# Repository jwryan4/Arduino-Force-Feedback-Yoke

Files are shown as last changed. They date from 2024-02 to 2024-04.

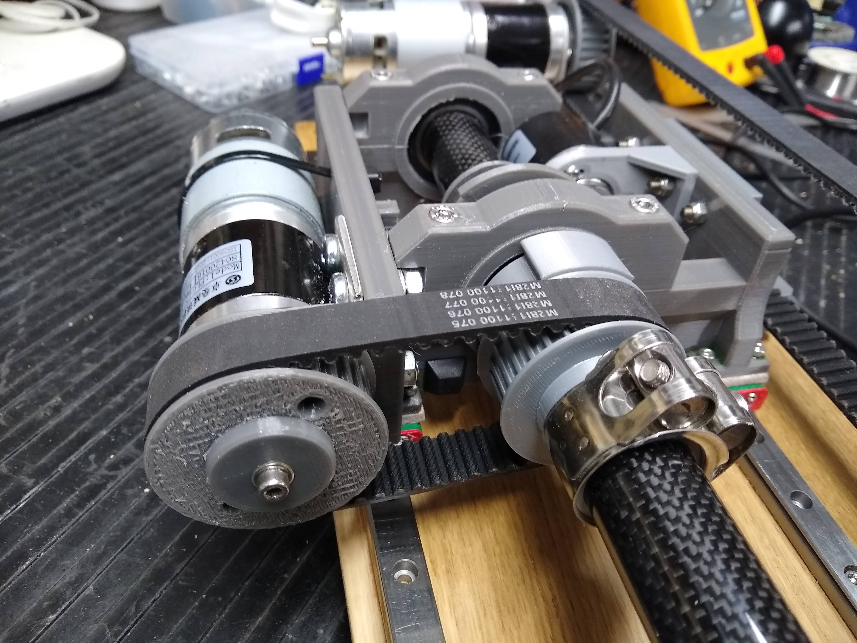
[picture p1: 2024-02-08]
Photos/IMG_20231003_192117274.jpg

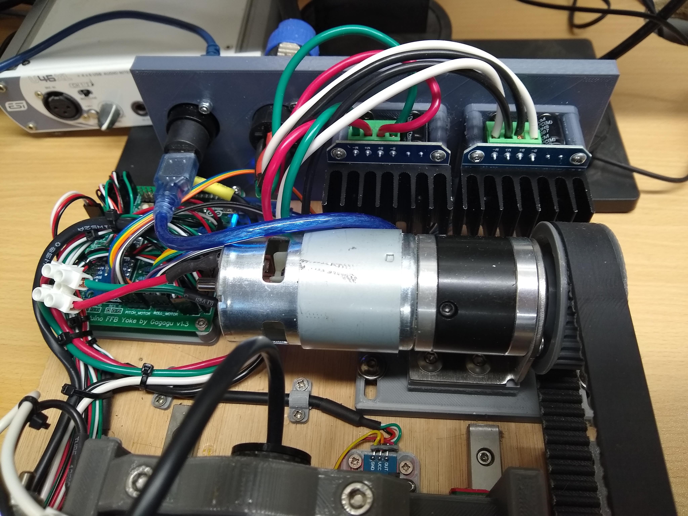
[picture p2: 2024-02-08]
Photos/IMG_20240125_142316894.jpg

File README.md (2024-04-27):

# Arduino-Force-Feedback-Yoke "NOT THE ORIGNIAL PROJECT!! THAT'S HERE: https://github.com/jwryan4/Arduino-Force-Feedback-Yoke"
CAD Files for GAGAGU FFB Flight Sim Yoke

I am going to try and update as much as I can so that We have everything needed to complete the new V2 project. 

I am not the create nor the designer of this project all credit goes to the wonderful creators https://github.com/jwryan4 & https://github.com/gagagu

They have done some amazing work and this is just me trying to make it easier for us as plebs to create their awesome project

One of the massive changes is the arrival of the rotary encoders. 

I am not as smart as I would like to be when it comes to making theses kinds of things but JR4 is, the way you need to wire the new encoders to the exsiting circutry is as follows and I Quote:

"There is no need for centre posn sensors as the rotary encoders provide better tracking accuracy than previous versions (v1.x). Use the same pcb. Rotary encoders connect to pin headers ROLL 1/ROLL 2 and PITCH1/PITCH2.  My encoders have 4 wires, BLK (gnd), RED (+V), GRN (phase1 out), WHT (phase2 out).  Connect GRN to PITCH1/ROLL1, WHT to PITCH2/ROLL2." - JR4

This one line of information is what should be able to take you from V1.3 to V2!!

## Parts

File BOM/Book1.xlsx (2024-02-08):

BOM List for GAGAGU FFB Yoke version 2
Description | Qty | Detail | Hyperlink | Price | Total
 |  |  |  | £
Mechanical
RS775 motor | 2 | Available from Amazon (same spec available many suppliers ) | Link (https://www.amazon.co.uk/gp/product/B075D85KVV/ref=ppx_yo_dt_b_search_asin_title?ie=UTF8&psc=1) | 12.99 | 25.98
Motor Bracket |  | Available from Aliexpress | Link (https://www.aliexpress.com/item/1005003394995769.html?spm=a2g0o.cart.0.0.5f2738daYltizJ&mp=1) | 8.39 | 8.39
Planetary Gearbox, Pitch (see note 1 below) | 1 | PLG42-16G, 42mm, 4:1, 10mm keyed output shaft with 5mm pinion gear for input | Link (https://www.amazon.co.uk/dp/B0BTY4VBBQ/?coliid=I15R9M6IFE6G61&colid=11U0ZQFTY1AUE) | 61.21 | 61.21
Planetary Gearbox, Roll (see note 1 below) | 1 | PLG42-16G, 42mm, 20:1, 10mm keyed output shaft with 5mm pinion gear for input | Link (https://www.amazon.co.uk/dp/B0BVQML11F/?coliid=I15R9M6IFE6G61&colid=11U0ZQFTY1AUE) | 74.66 | 74.66
Precision Quadrature Rotary Encoder | 2 | 600ppr (various suppliers) | Link (https://www.ebay.co.uk/itm/204516788210) | 12.72 | 25.44
Corbon Fibre Yoke Column | 1 | 25mm OD, 23mm ID, 300mm length | Link (https://www.amazon.co.uk/gp/product/B017XEAMUI/ref=ppx_yo_dt_b_search_asin_title?ie=UTF8&psc=1) | 14.19 | 14.19
Yoke Column Bearing (pair) | 1 | 6905-2RS, 42mm OD, 25mm ID, 9mm width | Link (sold as a pair) (https://www.ebay.co.uk/itm/266121767350) | 4.00 | 4.00
Pitch Encoder Belt Bearing (pair) | 1 | 61805-2RS, 32mm OD, 37mm ID, 7mm width | Link (sold as a pair) (https://www.ebay.co.uk/itm/266109732777) | 4.95 | 4.95
Linear Rails (see note 2 below) | 2 | Linear Rail MGN12C x 300mm (available from many suppliers) | Link (https://www.ebay.co.uk/itm/353965723573) | 17.00 | 34.00
Additional Guide (Carriage) for Linear Rails | 2 | Bearing Block MGN12C | Link (https://www.ebay.co.uk/itm/185853523677) | 6.36 | 12.72
Pitch Belt | 1 | 850-5M-15 Timing Belt | Link (https://www.bearingsrus.co.uk/850-3m-15) | 7.87 | 7.87
Roll Belt | 1 | 305-5M-15 Timing Belt | Link (https://www.bearingsrus.co.uk/305-3m-15) | 4.84 | 4.84
Roll Encoder Belt | 1 | 77T, 154mm, GT2, 6mm, 2mm pitch | Link (https://www.ebay.co.uk/itm/283194907394?var=586475426779) | 2.95 | 2.95
Picth Belt Clamp | 1 | Aluminium Timing Belt Clamp, HTD-5M 15 | Link (https://www.ebay.co.uk/itm/403912354720?var=673795213478) | 3.95 | 3.95
Yoke/ Roll drive pulley Column Clamp (pair) | 1 | Hose Clamp, Stainless Steel, 29-31mm | Link (sold as a pair) (https://www.ebay.co.uk/itm/203846963479?var=504299046223) | 9.02 | 9.02
Miscellaneous Items
Screws | Various | Price is approximate as various sizes/qty's required |  | 40.00 | 40.00
PLA+, GRY/BLK 2-pack | 1 |  | Link (https://www.amazon.co.uk/gp/product/B0B749Z8H1/ref=ppx_yo_dt_b_search_asin_title?ie=UTF8&th=1) | 38.99 | 38.99
Plywood Board, 18mm | 1 | Required for rigid base |  | 20.00 | 20.00
Plywood coard, 9mm | 1 | Required for U-shaped outer case |  | 15.00 | 15.00
 |  |  |  |  | 0.00
Electronic |  |  |  |  | 0.00
Arduino Micro | 1 |  | Link (https://www.amazon.co.uk/gp/product/B00AFY2S56/ref=ppx_yo_dt_b_search_asin_title?ie=UTF8&th=1) | 25.00 | 25.00
BTS7960 H-Bridge Motor Drivers (pair) | 1 |  | Link (sold as a pair) (https://www.amazon.co.uk/gp/product/B098WYZ9DP/ref=ppx_yo_dt_b_search_asin_title?ie=UTF8&psc=1) | 14.00 | 14.00
Power Supply, SMPS, 24 Volt, 10 Amp | 1 |  | Link (https://www.amazon.co.uk/gp/product/B09YRF3ZHR/ref=ppx_yo_dt_b_search_asin_title?ie=UTF8&psc=1) | 16.99 | 16.99
Note 1: Planetary Gearboxes
My planetary gearboxes were sourced from Aliexpress. However, the item is no longer listed (as of Jan 2024). The links above seem to be the same product from Amazon UK but at twice the price. Please be aware that you buy at your own risk. |  | I used gearboxes with a 10mm keyed output shaft because I think that a standard 6.35mm D or 8mm shaft would cause 3D printed pulleys to fail (I used PLA+). Shaft adaptors for smaller diameters are available from eBay if required. Please note that the motor pulley STL file may require modification to ensure good fit with your gear output shaft/adaptor. | Output Shaft Adaptor (https://www.ebay.co.uk/itm/155829523711)
Note 2: Linear Rails
Supplier will not ship to UK

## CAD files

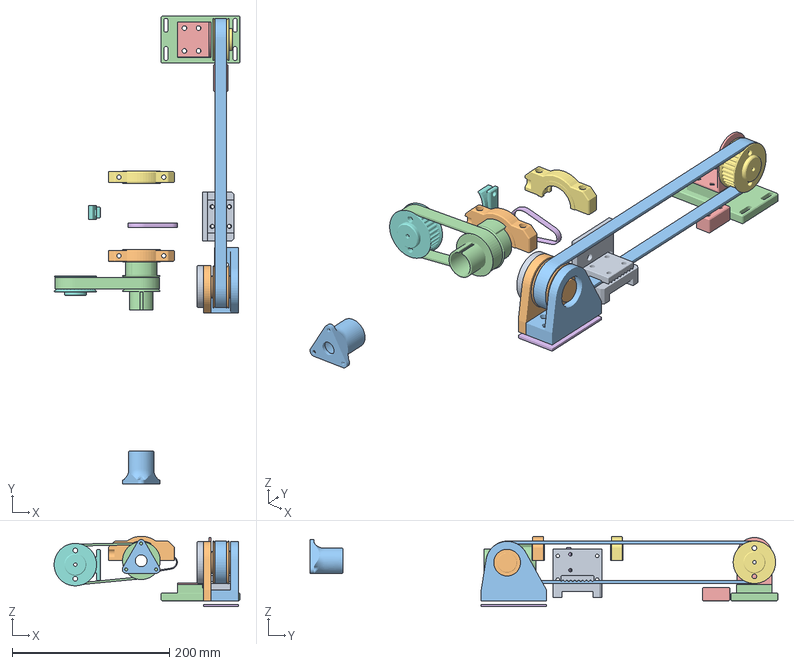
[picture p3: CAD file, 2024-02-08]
FFB_Yoke_Assembly_v2.FCStd
236.2 x 595.2 x 89.4 mm
Frame_Pitch_Belt_Clamp
Pitch_Belt
Roll_Belt
Roll Motor Mount
Roll_Encoder_Belt
Rear_Yoke_Column_Upper_Mount
Roll_Motor_Rear_Mount
Pitch Encoder Spacer
Pitch Encoder Mount
Pitch Encoder Pulley Mount
Pitch_Motor_Mount
Pitch_Rear_Stop
Pitch Encoder Pulley Mount001
HTD 32 5M 15 Pulley v8
HTD 32 5M 15 Pulley v009
Clamping_Plate v1
Pitch_Encoder_Pulley_5_15_32t v4
CadetYokev3 (1) v6
28_5M_15_Yoke_Column_Pulley v24

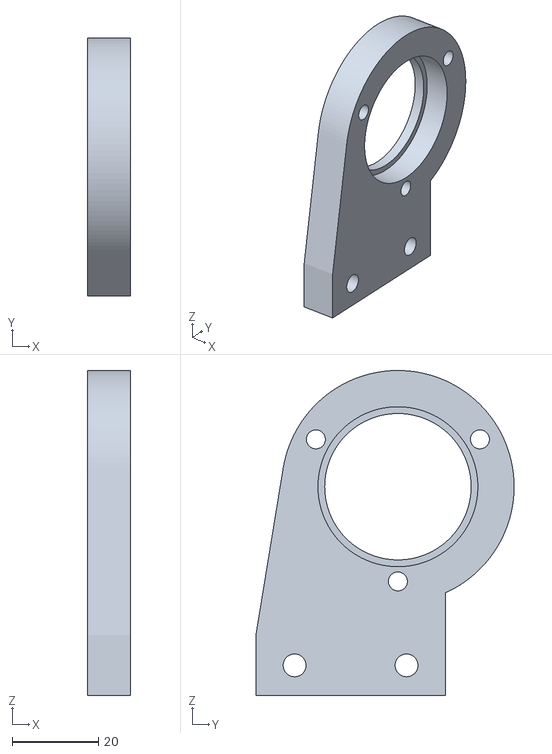
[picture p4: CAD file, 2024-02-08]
STL Files/FFB_Yoke_Assembly_v2-Pitch_Pulley_Mount_AssyPitch Encoder Mount.stl
10.0 x 60.0 x 75.5

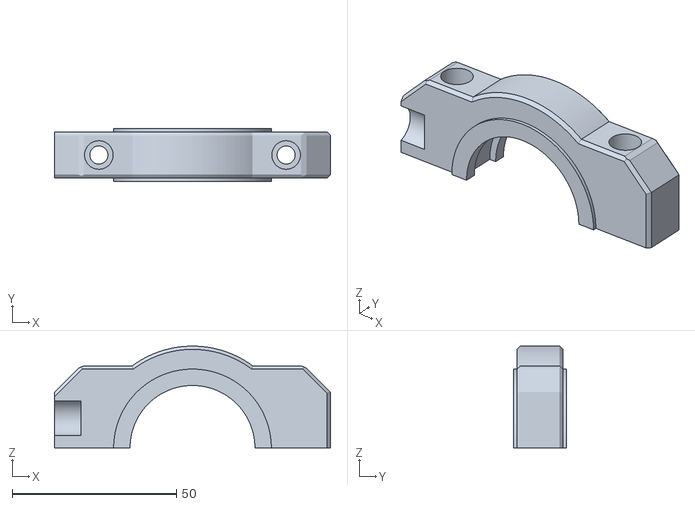
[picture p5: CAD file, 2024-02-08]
STL Files/FFB_Yoke_Assembly_v2-Rear_Yoke_Shaft_Housing_Top.stl
84.0 x 16.0 x 31.0

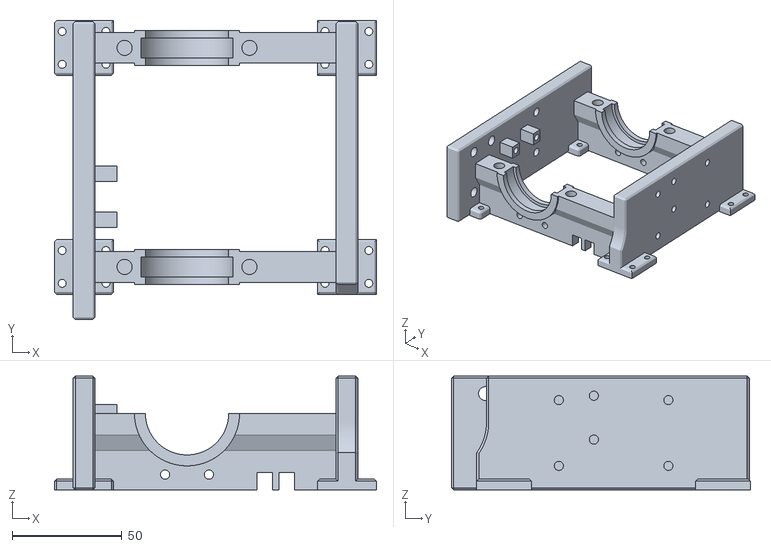
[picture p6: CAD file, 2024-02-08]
STL Files/FFB_Yoke_Assembly_v2-Frame.stl
147.0 x 136.5 x 52.0

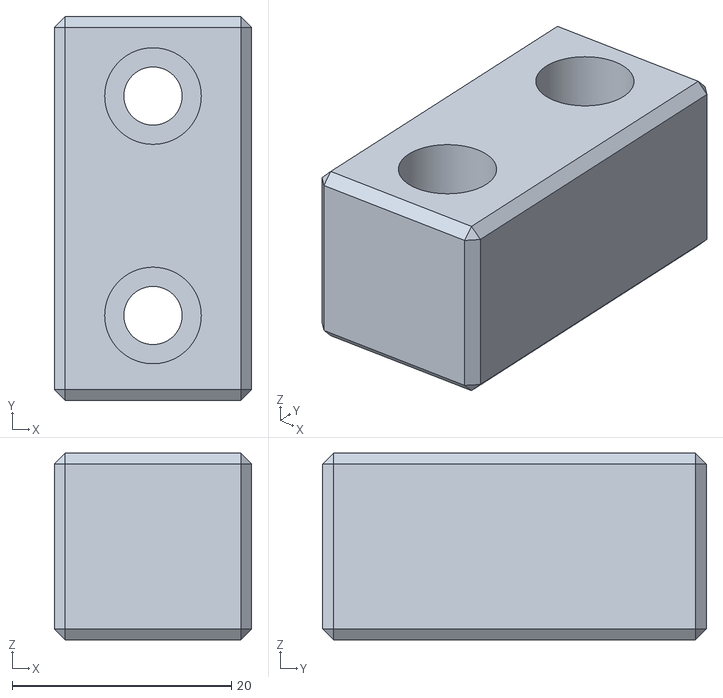
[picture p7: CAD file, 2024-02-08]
STL Files/FFB_Yoke_Assembly_v2-Pitch_Rear_Stop.stl
18.0 x 35.0 x 17.0

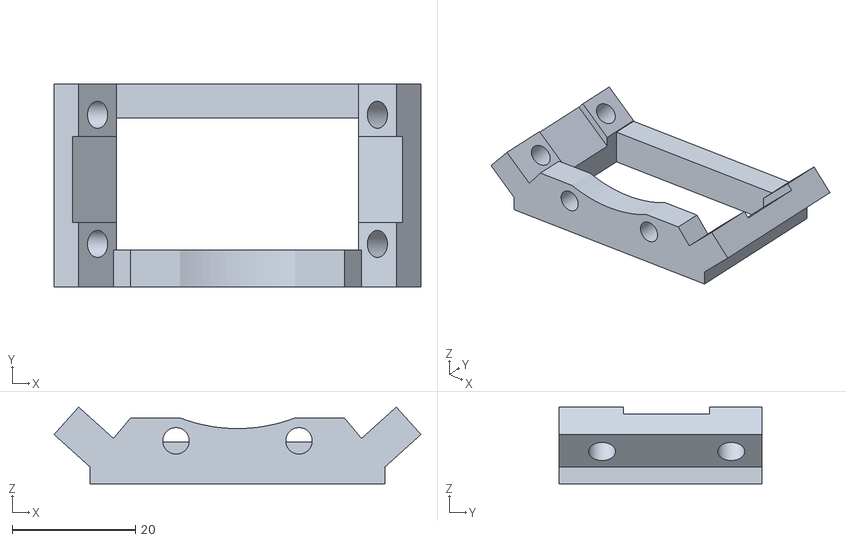
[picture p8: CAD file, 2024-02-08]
STL Files/FFB_Yoke_Assembly_v2-Frame_Roll_IR_Sensor_Mount.stl
59.7 x 33.0 x 12.5

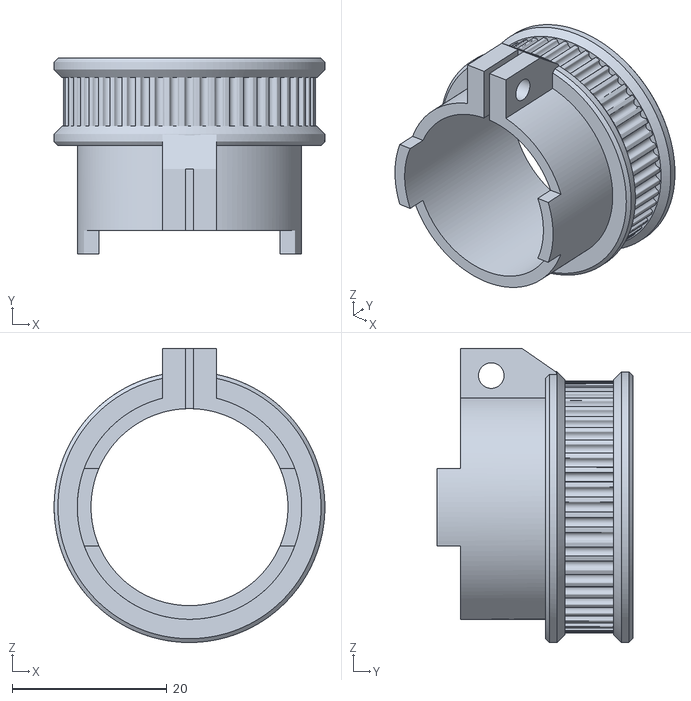
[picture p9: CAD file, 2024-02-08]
STL Files/FFB_Yoke_Assembly_v2-Yoke_Roll_Encoder_Pulley.stl
35.0 x 25.3 x 38.0

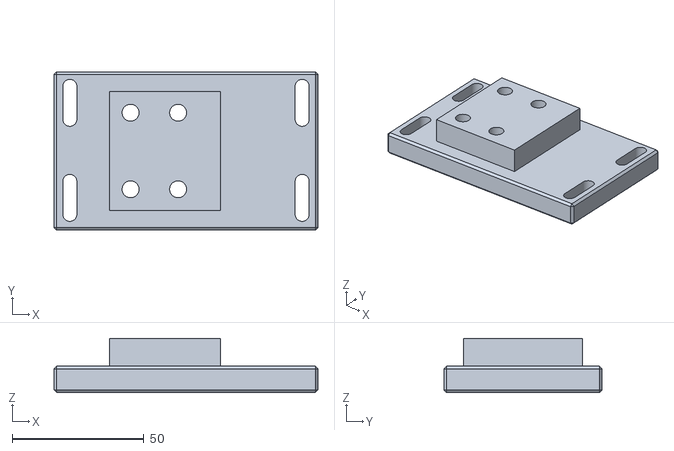
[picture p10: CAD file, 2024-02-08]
Misc STL Files/FFB_Yoke_Assembly_v2-Pitch_Motor_Mount.stl
100.0 x 60.0 x 20.5

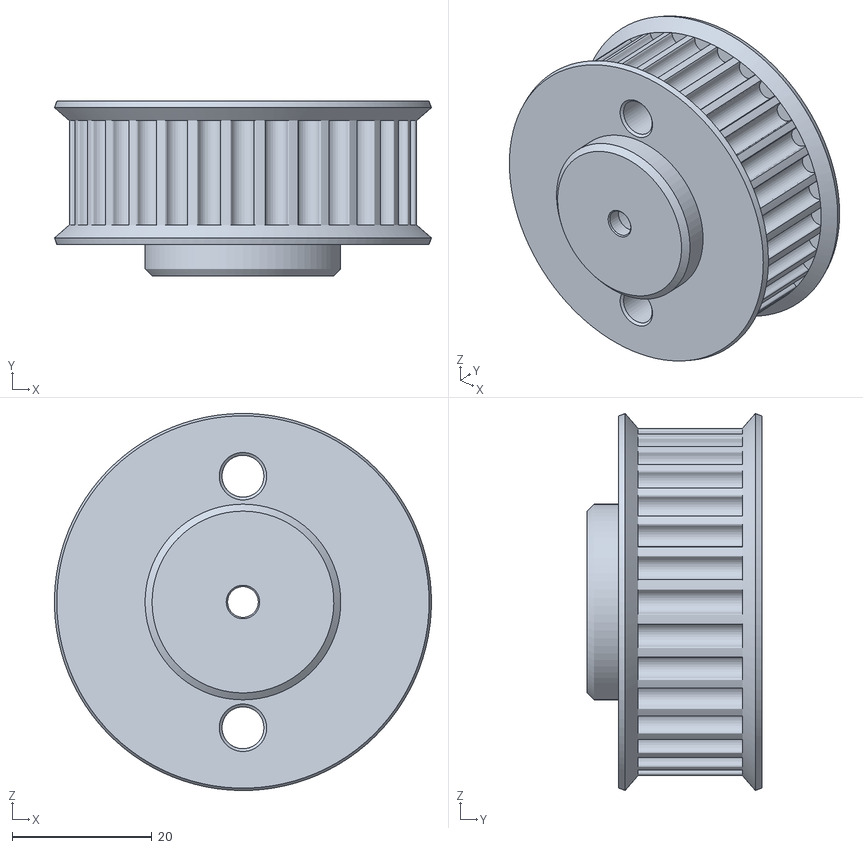
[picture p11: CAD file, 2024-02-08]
STL Files/FFB_Yoke_Assembly_v2-HTD 32 5M 15 Pulley v009.stl
53.9 x 25.0 x 53.9

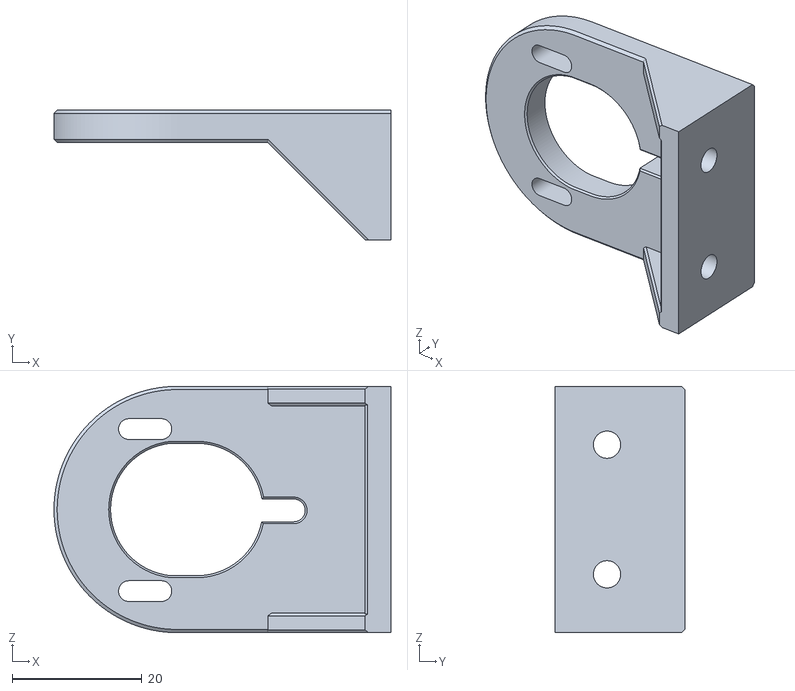
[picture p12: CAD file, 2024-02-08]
STL Files/FFB_Yoke_Assembly_v2-Roll_Encoder _Mount.stl
52.0 x 20.0 x 38.0

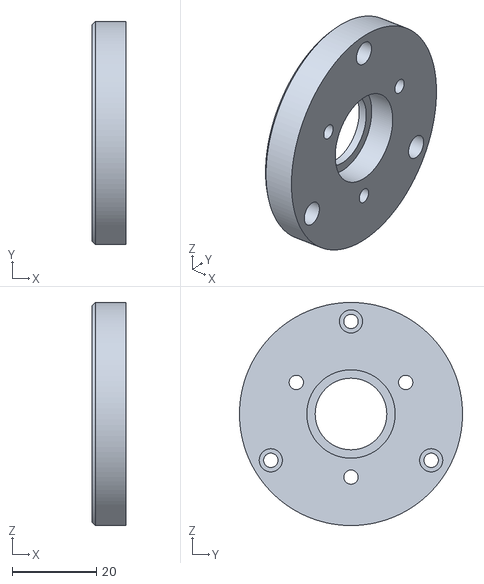
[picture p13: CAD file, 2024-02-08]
STL Files/FFB_Yoke_Assembly_v2-Pitch_Encoder_Spacer.stl
8.00 x 53.0 x 53.0

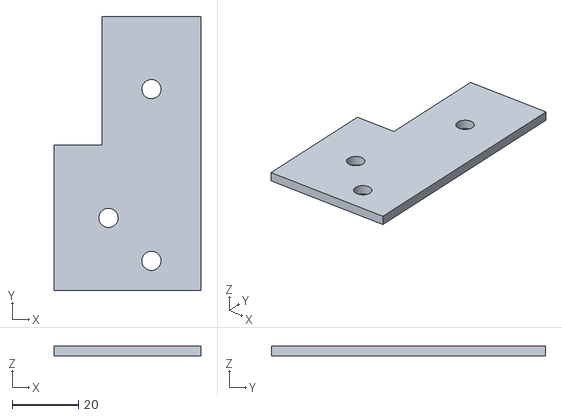
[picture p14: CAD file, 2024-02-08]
STL Files/FFB_Yoke_Assembly_v2-Pitch Encoder Pulley Mount001.stl
44.5 x 83.0 x 3.00

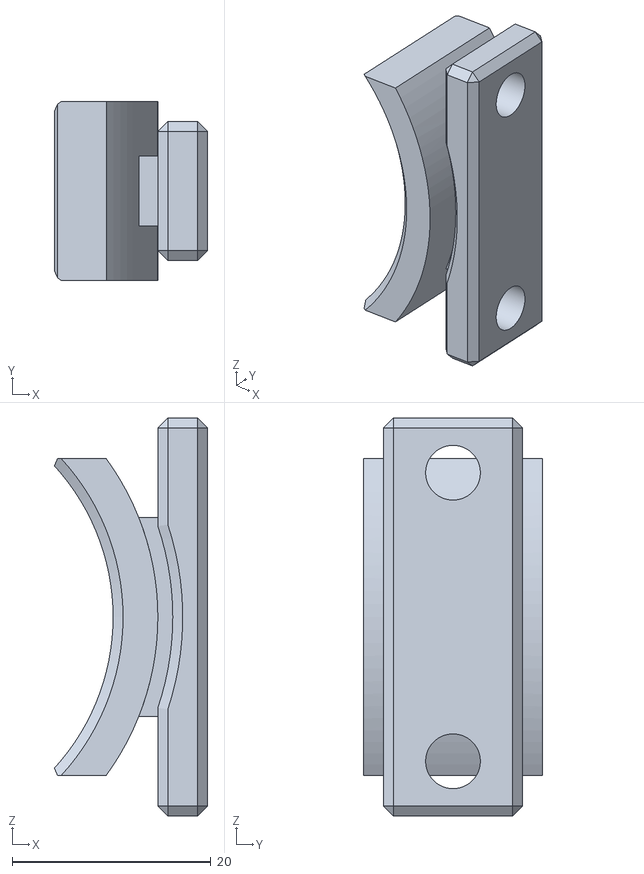
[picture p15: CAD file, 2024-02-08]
STL Files/FFB_Yoke_Assembly_v2-Roll_Motor_Rear_Mount.stl
15.4 x 18.0 x 40.0

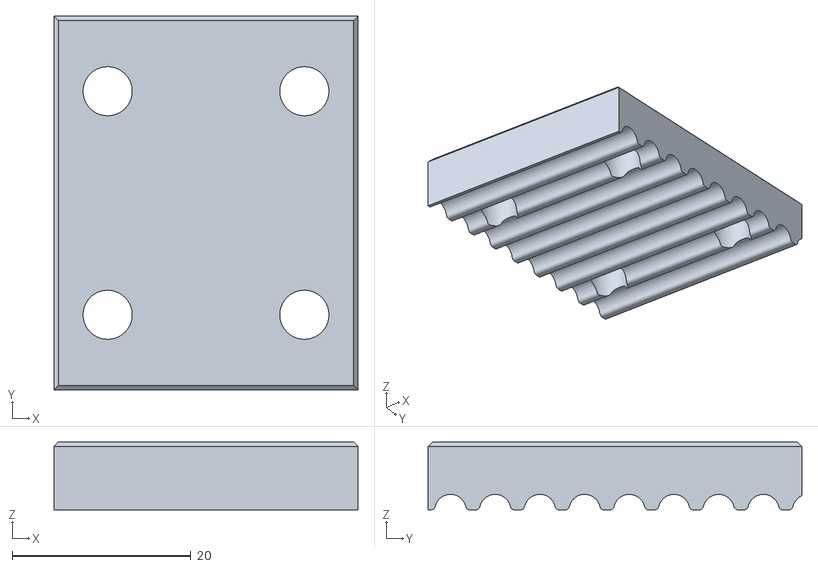
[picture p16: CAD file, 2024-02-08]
STL Files/FFB_Yoke_Assembly_v2-Clamping_Plate v1.stl
34.0 x 41.8 x 7.60

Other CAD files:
STL Files/FFB_Yoke_Assembly_v2-HTD 32 5M 15 Pulley v8.stl
STL Files/FFB_Yoke_Assembly_v2-Pitch_Motor_Mount.stl
STL Files/FFB_Yoke_Assembly_v2-Yoke_Mount.stl
STL Files/FFB_Yoke_Assembly_v2-Roll_Limit_Stop.stl
Converted2Stls/2Cable_Clip_4_7mm.stl
Converted2Stls/3Cable_Clip_4_7mm.stl
Converted2Stls/BTS7960_PCB_Frame.stl
Converted2Stls/BTS7960_PCB_Frame_35mmStandoff.stl
Converted2Stls/Cable_Clip_4_7mm.stl
Converted2Stls/Cable_Support.stl
Converted2Stls/Display_Frame.stl
Converted2Stls/Limit_Sensor_Bracket.stl
Converted2Stls/PCB_Frame.stl
Converted2Stls/PSU_Box_V2.stl
Converted2Stls/Pitch_Pulley_Base.stl
Converted2Stls/Rail_Spacers.stl
Converted2Stls/Rear_Panel.stl
Fusion 360 Pulleys/28_5M_15_Yoke_Column_Pulley v24.f3d
Fusion 360 Pulleys/HTD 32 5M 15 Pulley v8.f3d
Fusion 360 Pulleys/Pitch_Encoder_Pulley_V2 v6.f3d
Misc STL Files/28_5M_15_Yoke_Column_Pulley v24.stl
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

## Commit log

2024-02-08 Add files via upload
    CAD files for Version 2.0 of GAGAGU FFB Yoke Project
    https://github.com/gagagu/Arduino_FFB_Yoke/wiki
    Discord channel for further details.
    https://discord.com/channels/458198731972542465/982583059595550770
    Video demo on Youtube
    https://youtu.be/_BLexbrsTKU
    [28_5M_15_Yoke_Column_Pulley v24.f3d, 28_5M_15_Yoke_Column_Pulley v24.stl, 2Cable_Clip_4_7mm.FCStd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]
2024-04-26 Added Rail spacers needed to raise the main body
    Just some 2.7mm spacers, designed to be printed in TPU for flexibility. JR4 used foam pieces I thought I would try this instead.
    [Rail_Spacers.stl]
2024-04-26 Just a bunch of the files that weren't STLs
    Reformatted the files so they are in STL format.
    [2Cable_Clip_4_7mm.stl, 3Cable_Clip_4_7mm.stl, BTS7960_PCB_Frame.stl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]
2024-04-26 Fixed mistake
    [Rail_Spacers.stl]
